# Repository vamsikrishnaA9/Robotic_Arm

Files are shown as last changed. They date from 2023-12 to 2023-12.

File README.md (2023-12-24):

<!-- PROJECT SHIELDS -->
<!--
*** I'm using markdown "reference style" links for readability.
*** Reference links are enclosed in brackets [ ] instead of parentheses ( ).
*** See the bottom of this document for the declaration of the reference variables
*** for contributors-url, forks-url, etc. This is an optional, concise syntax you may use.
*** https://www.markdownguide.org/basic-syntax/#reference-style-links
-->
[][contributors-url]
[][license-url]
[][linkedin-url]

<!-- PROJECT LOGO -->
<br />
<div align="center">

  <h1 align="center">3 DOF Robotic Arm</h1>

</div>

<!-- TABLE OF CONTENTS -->
<details>
  <summary>Table of Contents</summary>
  <ol>
    <li>
      <a href="#about-the-project">About The Project</a>
    </li>
    <li>
      <a href="#getting-started">Getting Started</a>
     <ul>
      <li><a href="#Nema 17">NEMA 17</a></li>
      <li><a href="#A4988">A4988</a></li>
       <li><a href="#Iinverse Kinematics">Inverse Kinematics</a></li>
      <li><a href="#prerequisites">Prerequisites</a></li>
      <li><a href="#installation">Installation</a></li>
      </ul>
    </li>
    <li><a href="#usage">Usage</a></li>
    <li><a href="#contributing">Contributing</a></li>
    <li><a href="#license">License</a></li>
    <li><a href="#contact">Contact</a></li>
   
  </ol>
</details>

<!-- ABOUT THE PROJECT -->
## About The Project

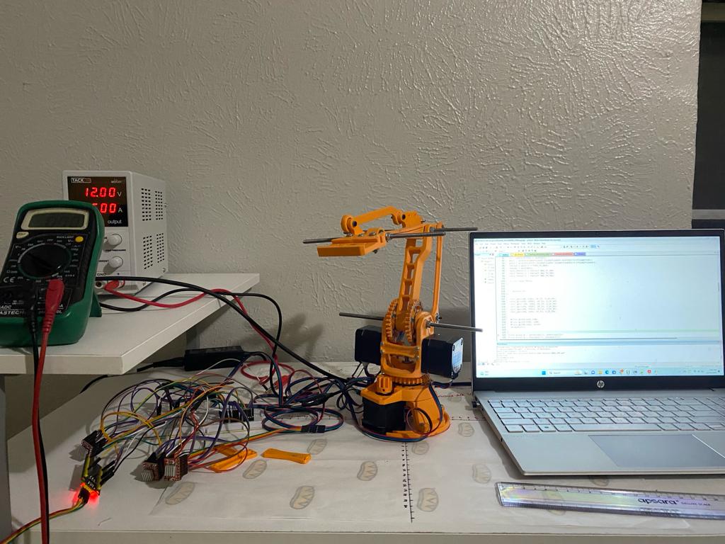
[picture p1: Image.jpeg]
Product Name Screen Shot
[](https://example.com) 

Welcome to 3-DOF Robotic Arm project!. This repository houses all the software design files, documentaion and PCB files for the Robotic Arm.
This Robitic Arm is equipped with 3 rotational joints providing adaptability and flexibility in moving 3-D space.This project includes Mechanical CAD design source files were originally forked from the repository 
maintained by `Florin Tobler`, which can be found at [https://github.com/ftobler/robotArm](https://github.com/ftobler/robotArm).

This robot was developed using NEMA 17 stepper motors and 3D printed with PLA plastic. The Maximum height can go up to `250mm` and the Maximum length can reach `200mm` horizontally. Due to the nature of the PLA material, the Robot can bear a 250gms payload.
Different sets of bearings and screws are used for smooth joint movements.
Implemented inverse kinematics to calculate all the robot joints and made the stepper motors rotate according to the joint angles.

This project was built using embedded C. 

<!-- GETTING STARTED -->
## Getting Started

## NEMA 17  
It is the most commonly used stepper motor sized in various applications including 3D printers various CNC machines and Robotic arms. NEMA 17 has a standard frame size of 1.7 inches. The motor is a Bipolar (4-wire) configuration. NEMA 17 motors typically have a step angle of 1.8 degrees per step. To make one revolution it takes 200 steps to complete and make it suitable for high-precision applications. 
## A4988
It is the specific motor driver, especially for NEMA 17 motors. The driver has a maximum current limit of 2A. A4988 driver has micro-stepping features which are essential in operating the NEMA 17 in high precision.<br>
`Full Mode		200 steps` <br>
`Half Mode		400 steps` <br>
`1/4 Mode		800 steps`  <br>
`1/8 Mode		1600 steps` <br>
`1/16 Mode		3200 steps`.

## Inverse Kinematics
Inverse kinematics is a mathematical approach used in robotics to determine the joint configurations required to position a robotic arm or end-effector at a specific location and orientation in three-dimensional space.
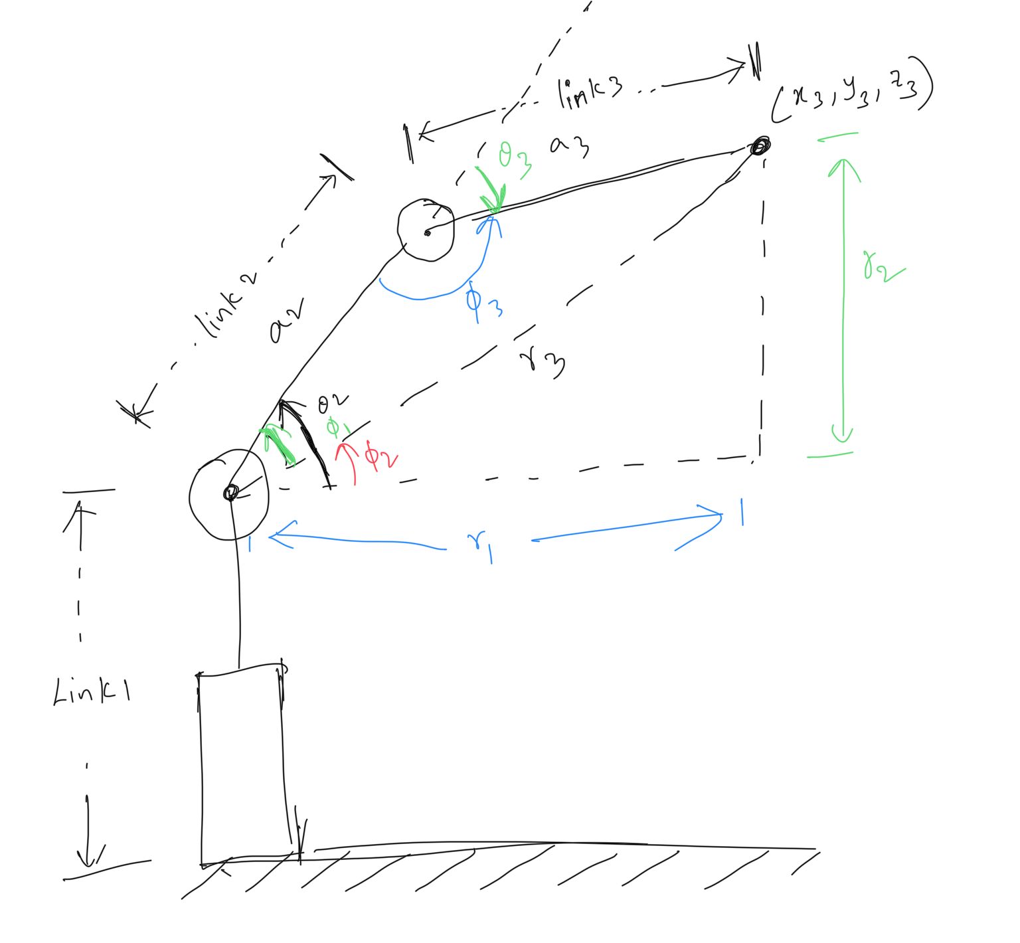
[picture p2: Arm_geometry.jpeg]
Arm geometery


### Prerequisites

`Software - Keil u vision` <br> 
`Hardware - STM32F1 microcontroller` <br> 
            &emsp;&emsp;&emsp;&emsp;&emsp; `A4988 Motor drivers` <br> 
            &emsp;&emsp;&emsp;&emsp;&emsp; `NEMA 17 Stepper motors` <br> 
            &emsp;&emsp;&emsp;&emsp;&emsp; `Power supply (0-30V)`

### Installation

1. Clone the repo
   ```sh
   git clone https://github.com/vamsikrishnaA9/Robotic_Arm.git
   ```
2. Connect the circuit as specified.

<!-- USAGE EXAMPLES -->
## Usage

_1. double *inv_KE(double X3, double Y3, double Z3)_ <br> 
This function solves the inverse kinematics for the given coordinates `X3, Y3, Z3` and returns the pointer of 3 joint angles. <br>

_2. void Robot_target(double* Out)_ <br> 
This function sets the target coordinates based on the previous position of the Arm robot. <br> 

_3. void Robot_move(double angle, int type)_ <br> 
This function rotates the stepper motors at the desired angle.

<!-- CONTRIBUTING -->
## Contributing

Contributions are what makes the open-source community such an amazing place to learn, inspire, and create. Any contributions you make are **greatly appreciated**.

If you have a suggestion that would make this better, please fork the repo and create a pull request. You can also simply open an issue with the tag "enhancement".
Don't forget to give the project a star! Thanks again!

1. Fork the Project
2. Create your Feature Branch (`git checkout -b feature/AmazingFeature`)
3. Commit your Changes (`git commit -m 'Add some AmazingFeature'`)
4. Push to the Branch (`git push origin feature/AmazingFeature`)
5. Open a Pull Request

<!-- LICENSE -->
## License

Distributed under the MIT License. See `LICENSE.txt` for more information.

<!-- CONTACT -->
## Contact

Vamsi Krishna - [vamsi.vk1596@gmail.com](vamsi.vk1596@gmail.com) 

Project Link: [https://github.com/vamsikrishnaA9/Robotic_Arm](https://github.com/vamsikrishnaA9/Robotic_Arm)

<!-- MARKDOWN LINKS & IMAGES -->
<!-- https://www.markdownguide.org/basic-syntax/#reference-style-links -->
[contributors-shield]: https://img.shields.io/github/contributors/othneildrew/Best-README-Template.svg?style=for-the-badge
[contributors-url]: https://github.com/vamsikrishnaA9/Robotic_Arm/graphs/contributors
[license-shield]: https://img.shields.io/github/license/othneildrew/Best-README-Template.svg?style=for-the-badge
[license-url]: https://github.com/vamsikrishnaA9/Robotic_Arm/blob/main/LICENSE.txt
[linkedin-shield]: https://img.shields.io/badge/-LinkedIn-black.svg?style=for-the-badge&logo=linkedin&colorB=555
[linkedin-url]: https://www.linkedin.com/in/vamsikrishna112/
[product-screenshot]: /Image.jpeg
[Kinematics_diagram]: /Arm_geometry.jpeg

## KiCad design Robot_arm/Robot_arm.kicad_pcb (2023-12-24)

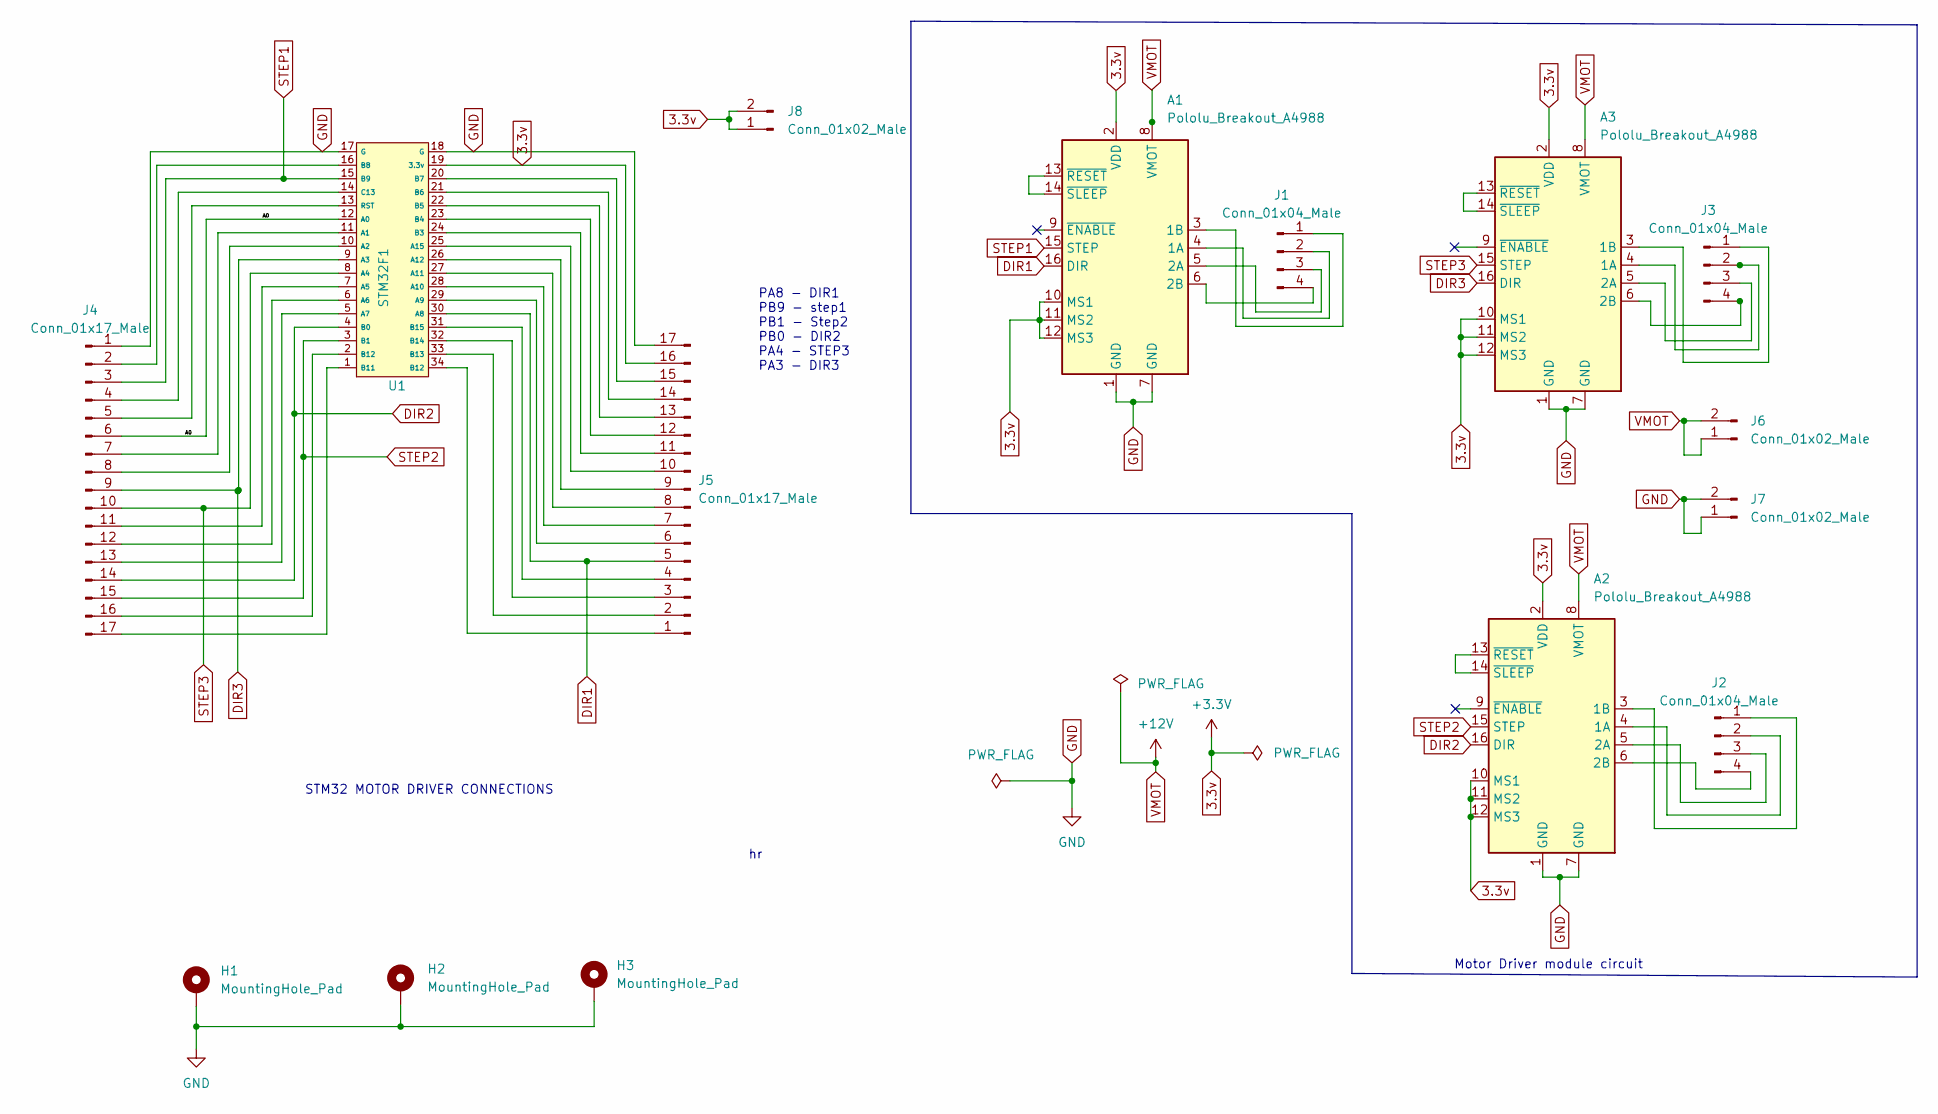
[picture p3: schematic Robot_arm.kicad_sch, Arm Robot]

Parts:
A1, A2, A3: Pololu_Breakout_A4988; Pololu_Breakout-16_15.2x20.3mm
H1, H2, H3: MountingHole_Pad; MountingHole_3.2mm_M3_Pad_Via
J1, J2, J3: Conn_01x04_Male; PinHeader_1x04_P2.54mm_Vertical
J4, J5: Conn_01x17_Male; PinHeader_1x17_P2.54mm_Vertical
J6, J7, J8: Conn_01x02_Male; PinHeader_1x02_P2.54mm_Vertical
U1: STM32F1

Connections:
3.3v: A1.2 (VDD), A1.10 (MS1), A1.11 (MS2), A1.12 (MS3), A2.2 (VDD), A2.10 (MS1), A2.11 (MS2), A2.12 (MS3), A3.2 (VDD), A3.10 (MS1), A3.11 (MS2), A3.12 (MS3), J5.16, J8.1, J8.2, U1.19 (3.3v)
/A0: J4.6, U1.12 (A0)
DIR1: A1.16 (DIR), J5.5, U1.30 (A8)
DIR2: A2.16 (DIR), J4.14, U1.4 (B0)
DIR3: A3.16 (DIR), J4.9, U1.9 (A3)
unnamed: A1.3 (1B), J1.1
unnamed: A1.4 (1A), J1.2
unnamed: A1.5 (2A), J1.3
unnamed: A1.6 (2B), J1.4
unnamed: A1.13 (~RESET), A1.14 (~SLEEP)
unnamed: A2.3 (1B), J2.1
unnamed: A2.4 (1A), J2.2
unnamed: A2.5 (2A), J2.3
unnamed: A2.6 (2B), J2.4
unnamed: A2.13 (~RESET), A2.14 (~SLEEP)
unnamed: A3.3 (1B), J3.1
unnamed: A3.4 (1A), J3.2
unnamed: A3.5 (2A), J3.3
unnamed: A3.6 (2B), J3.4
unnamed: A3.13 (~RESET), A3.14 (~SLEEP)
unnamed: J4.2, U1.16 (B8)
unnamed: J4.4, U1.14 (C13)
unnamed: J4.5, U1.13 (RST)
unnamed: J4.7, U1.11 (A1)
unnamed: J4.8, U1.10 (A2)
unnamed: J4.11, U1.7 (A5)
unnamed: J4.12, U1.6 (A6)
unnamed: J4.13, U1.5 (A7)
unnamed: J4.16, U1.2 (B12)
unnamed: J4.17, U1.1 (B11)
unnamed: J5.1, U1.34 (B12)
unnamed: J5.2, U1.33 (B13)
unnamed: J5.3, U1.32 (B14)
unnamed: J5.4, U1.31 (B15)
unnamed: J5.6, U1.29 (A9)
unnamed: J5.7, U1.28 (A10)
unnamed: J5.8, U1.27 (A11)
unnamed: J5.9, U1.26 (A12)
unnamed: J5.10, U1.25 (A15)
unnamed: J5.11, U1.24 (B3)
unnamed: J5.12, U1.23 (B4)
unnamed: J5.13, U1.22 (B5)
unnamed: J5.14, U1.21 (B6)
unnamed: J5.15, U1.20 (B7)
STEP1: A1.15 (STEP), J4.3, U1.15 (B9)
STEP2: A2.15 (STEP), J4.15, U1.3 (B1)
STEP3: A3.15 (STEP), J4.10, U1.8 (A4)
VMOT: A1.8 (VMOT), A2.8 (VMOT), A3.8 (VMOT), J6.1, J6.2

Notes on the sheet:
Motor Driver module circuit
PA8 - DIR1 PB9 - step1 PB1 - Step2 PB0 - DIR2 PA4 - STEP3 PA3 - DIR3
STM32 MOTOR DRIVER CONNECTIONS

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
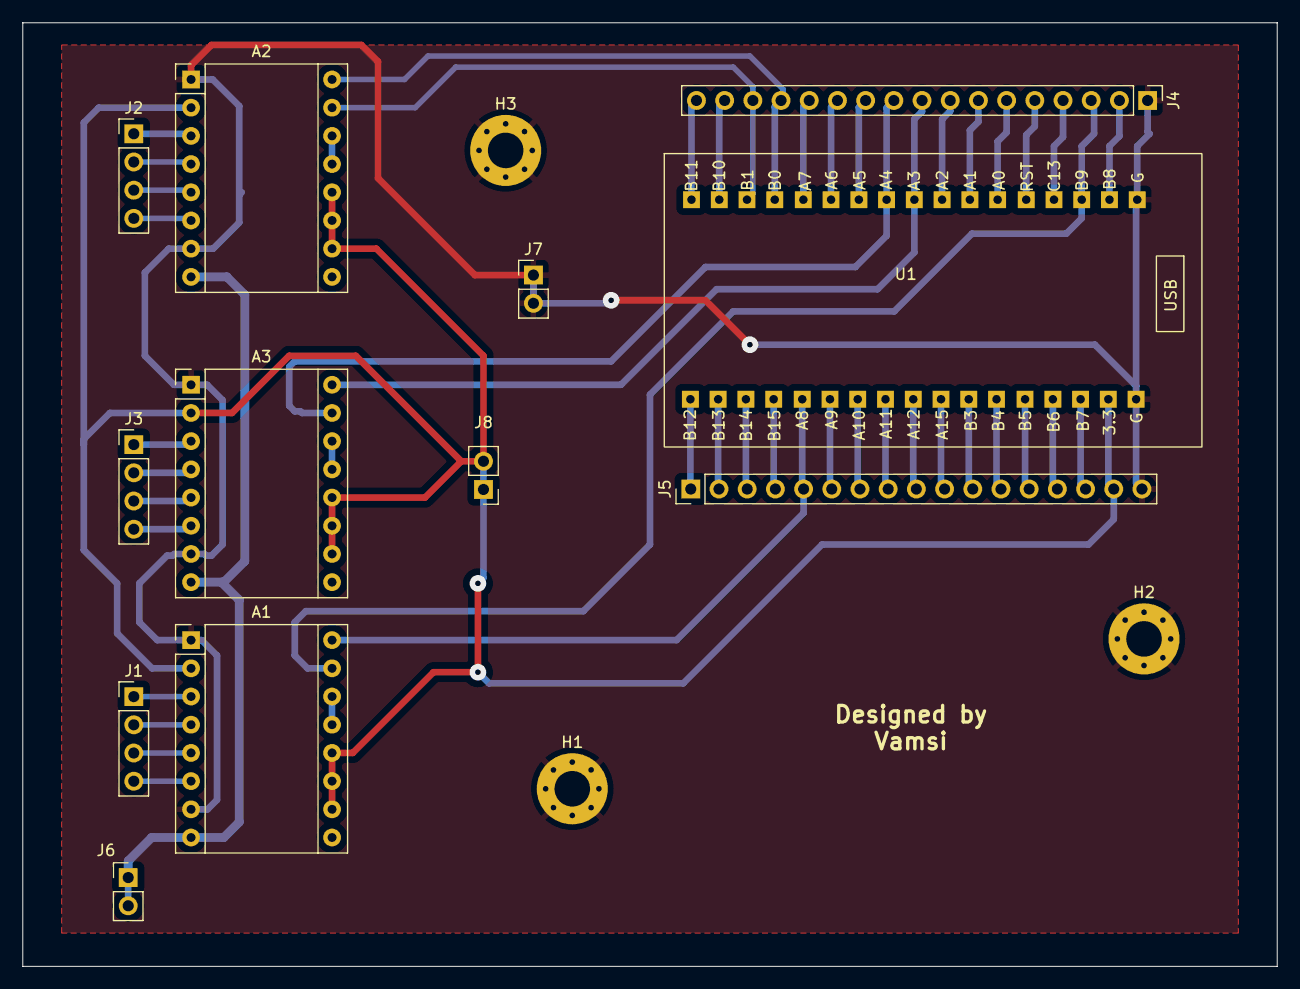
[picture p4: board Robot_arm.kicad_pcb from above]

Board: 2 copper layers, 113.0 x 85.0 mm, 15 parts (0 on the bottom side), 49 nets.

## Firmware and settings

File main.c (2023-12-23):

#include "gp_drive.h"
#include "stm32f10x.h"
#include "Delay.h"
#include "stdint.h"
#include "math.h"



#define DIR1 8
#define STEP1 9
#define DIR2 0
#define STEP2 1
#define DIR3 3
#define STEP3 4

#define PI 3.141592625
#define RAD_TO_DEG 180/PI
#define DEG_TO_RAD PI/180

//double X3,Y3,Z3;
 
static double angle_1 = 0;
static double angle_2 = 0;
static double angle_3 =0;

/*
float init_Angle1 = 0;
float	init_Angle2 = 0;  
float	init_Angle3 = 0;
*/

static double link1= 122;
static double link2 = 120;
static double  link3 = 120;
static double X1_3, Y1_3, Z1_3;
//static double r1,r2,r3;
//double theta1,theta2,theta3;
//double phi1,phi2,phi3;

 int num_steps = 50;
	
static double targ_Theta[3];
static double *Out;
static double present[3];
static double previous[3];
//static double offset[3];
void Robot_pos(void);	
double *inv_KE(double X3, double Y3, double Z3);
void lower_Motor(double angle);
void left_Motor(double angle);
void right_Motor(double angle);
void Robot_move(double angle, int type);
void Robot_target(double* Out);

//Point Linear_interpolation(Point p1, Point p2, double t);


typedef struct {
    double x;
    double y;
} Point;


Point linear_interpolation(Point p1, Point p2, double t) {
    Point interpolated_point;
    interpolated_point.x = p1.x + (p2.x - p1.x) * t;
    interpolated_point.y = p1.y + (p2.y - p1.y) * t;
    return interpolated_point;
}

void Robot_pos(void){
	
	angle_1 = present[0]- previous[0];
	angle_2 = present[1]-previous[1];
	angle_3 = present[2]-previous[2];
		
}



double *inv_KE( double X3,  double Y3, double Z3){
	
	double theta1 =0; double theta2=0; double theta3 =0; double phi1=0; double phi2=0; double phi3=0;
	X1_3 = X3;
	Y1_3 = Y3;
	Z1_3 = Z3;
	double r1,r2,r3;
	theta1 = atan2(Y3,X3);
	r1 = sqrt((X3*X3) + (Y3*Y3));
	r2 = Z3 - link1;
	phi2 = atan2(r2,r1);
	r3 = sqrt((r1*r1) + (r2*r2));
	phi1 = acos(((link3*link3)-(link2*link2)-(r3*r3))/(-2*link2*r3));
	phi3 = acos(((r3*r3)-(link2*link2)-(link3*link3))/(-2*link2*link3));
	theta3 = phi3-(180*DEG_TO_RAD);
	theta2 = phi2+phi1;
	targ_Theta[0] = theta1* RAD_TO_DEG;
	targ_Theta[1] = theta2* RAD_TO_DEG;
	targ_Theta[2] = theta3* RAD_TO_DEG;
	
	return targ_Theta;
}


int main(void)
{
	
	init_gpio(PA, DIR1, OP_50, O_GP_PP);
	init_gpio(PB, STEP1, OP_50, O_GP_PP);
	init_gpio (PB, DIR2, OP_50, O_GP_PP);
	init_gpio(PB, STEP2, OP_50, O_GP_PP);
	init_gpio(PA, STEP3, OP_50, O_GP_PP);
	init_gpio(PA, DIR3, OP_50, O_GP_PP);
	
	
	Write_gp(PA,DIR1,LOW);
	Write_gp(PB,DIR2, LOW);
	Write_gp(PA,DIR3, HIGH);
	DelayInit();
	

Point point_A = {previous[1], previous[2]};
Point point_B = {present[1], present[2]};


Out = inv_KE(120,70, 80);
Robot_target(Out);
Robot_pos();

Robot_move(angle_1,1);
Robot_move(angle_2,2);
Robot_move(angle_3,3);

DelayMs(4000);

Out = inv_KE(60, -70, 240); //119.57, -113.05 //119.5, -96.52
Robot_target(Out);
Robot_pos();

Robot_move(angle_1,1);
Robot_move(angle_2,2);
Robot_move(angle_3,3);

DelayMs(3000);

Out = inv_KE(120, 0, 80);
Robot_target(Out);
Robot_pos();

Robot_move(angle_1,1);
Robot_move(angle_3, 3);
Robot_move(angle_2,2);




//Robot_move(angle_2,2);  //-90   +ve in angle makes the right motor up wards i.e gear turns backwards, theta 2
// Robot_move(angle_3,3);  //90  -ve in angle makes the left motor downwards i.e gear turns forward. theta 3
 DelayMs(500);


 
	while(1){
		
}
}

void lower_Motor(double angle){
	int total = 11377;
	float small_ang = 360/angle;
	int value =(int)(total/small_ang) ;
		for(int i=0; i<value; i++){
		Write_gp(PB,STEP1,HIGH);
		//DelayMs(5);
		DelayUs(500);
		Write_gp(PB,STEP1,LOW);
		DelayUs(500); }
	
}

void left_Motor(double angle){	
int total = 11377;
float small_ang = 360/angle;
int value =(int)(total/small_ang);
for(int i=0; i<value; i++){
		Write_gp(PB,STEP2,HIGH);
		//DelayMs(5);
		DelayUs(500);
		Write_gp(PB,STEP2,LOW);
		DelayUs(500); }
	
}

void right_Motor(double angle){	
int total = 11377;
float small_ang = 360/angle;
int value =(int)(total/small_ang);
for(int i=0; i<value; i++){
		Write_gp(PA,STEP3,HIGH);
		//DelayMs(5);
		DelayUs(500);
		Write_gp(PA,STEP3,LOW);
		DelayUs(500); 
}
	
}

void Robot_move(double angle, int type){
	switch (type){
		case 1:
			if(angle <0 ){
		Write_gp(PA, DIR1, LOW);
		angle = -angle;
    lower_Motor(angle);}
	   else {
		Write_gp(PA, DIR1, HIGH);
		lower_Motor(angle);
	   }
	break;
		case 2:
		if(angle <0 ){
		Write_gp(PA, DIR3, LOW);
		angle = -angle;
    right_Motor(angle);}
	   else {
			 Write_gp(PA, DIR3, HIGH);
		right_Motor(angle);
	   }
	break;
		case 3:
		if(angle <0 ){
		angle = -angle;
	   Write_gp(PB, DIR2, HIGH);
     left_Motor(angle);}
	   else {
			 Write_gp(PB, DIR2, LOW);
		 left_Motor(angle);
	    }
		 break;
				
		default : break;
   			
					
}
	}

	void Robot_target(double* out){
	
	double temp[3];
	
	temp[0]= 0;
	temp[1]=0;
	temp[2]=0;
	
	previous[0] = present[0];
	previous[1] = present[1];
	previous[2] = present[2];
	
	if(X1_3>=120 | Z1_3>=120){
		//*(Out+2) =  fabs(90.00-fabs(*(Out+2)));
		*(Out+2) = fabs(*(Out+1)-fabs(90 - fabs(*(Out+2))));
		*(Out+2) = -(*(Out+2));
	}

   else if(X1_3 <120 & Z1_3 <120){
   *(Out+2) = fabs(90 - fabs(*(Out+2)));

   }
	temp[0] = *out;
	temp[1] = *(out+1);
	temp[2] = *(out+2);
	
	present[0]= temp[0];
	present[1]= temp[1];
	present[2] = temp[2];
 }	 

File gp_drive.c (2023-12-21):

#include "gp_drive.h"

void init_gpio(unsigned short port, unsigned short pin, unsigned short dir, unsigned short opt)
{
	volatile unsigned long *CR;
	unsigned short t_Pin =pin;
	unsigned offset = 0x00;
	
	if(pin>7){
		t_Pin -=8;
		offset = 0x01;
	}
	if(port ==1){
		RCC_APB2ENR |= 4;
		CR = (volatile unsigned long*) (&GPIO_A +offset);
	}
	else if(port==2){
		RCC_APB2ENR |= 8;
		CR = (volatile unsigned long*) (&GPIO_B + offset);
	}
	else if(port ==3){
		RCC_APB2ENR |= 0x10;
		CR = (volatile unsigned long*) (&GPIO_C + offset);
	}
	else if(port ==4){
		RCC_APB2ENR |= 0x20;
		CR = (volatile unsigned long*) (&GPIO_D + offset);
	}
	*CR &= ~(0xfu<<(t_Pin)*4);
	*CR |= ((dir <<(t_Pin)*4)|(opt<<(t_Pin*4+2)));		
}
int Read_gp(unsigned short port, unsigned short pin){
	
	volatile unsigned long *IDR;
	unsigned long offset = 0x02;
	int state;
	
  if(port ==1){
		IDR = (volatile unsigned long*) (&GPIO_A +offset);
	}
	if(port ==2){
		IDR = (volatile unsigned long*) (&GPIO_B +offset);
	}
	if(port ==3){
		IDR = (volatile unsigned long*) (&GPIO_C +offset);
	}
	if(port ==4){
		IDR = (volatile unsigned long*) (&GPIO_D +offset);
	}
	state = ((*IDR & (1<<pin))>>pin);
 	return state;	
}
void Write_gp(unsigned short port, unsigned short pin, unsigned state)
{
	volatile unsigned long *ODR;
	unsigned long offset = 0x03;
	
  if(port ==1){
		ODR = (volatile unsigned long*) (&GPIO_A +offset);
	}
 	if(port ==2){
		ODR = (volatile unsigned long*) (&GPIO_B +offset);
	}
	if(port ==3){
		ODR = (volatile unsigned long*) (&GPIO_C +offset);
	}
	if(port ==4){
		ODR = (volatile unsigned long*) (&GPIO_D +offset);
	}
	state ? (*ODR |= (state<<pin)) : (*ODR &= ~(1<<pin));	
}

	
